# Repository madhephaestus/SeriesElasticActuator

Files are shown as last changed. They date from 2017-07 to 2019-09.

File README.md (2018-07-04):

# SeriesElasticActuator
A cad generator for series elastic actuator modules

# Prerequisites

PC with Ubuntu 16.04 64 bit, 16gb of ram and a discrete graphics card with OpenGL 3.2+ support. 
# Start Simulation
To simulate and control the arm, after programming and calibrating the arm (see notes in FW comments, calibrating the zeros of the arm is lab one) run BowlerStudio
From here: 
http://commonwealthrobotics.com/#downloads
or directly from the PPA:
	sudo add-apt-repository ppa:webupd8team/java
	sudo add-apt-repository ppa:mad-hephaestus/commonwealthrobotics -y
	sudo apt-get update
	sudo apt-get remove arduino bowlerstudio 
	sudo apt-get install bowlerstudio oracle-java8-set-default oracle-java8-installer arduino-ide
To open the arm, run BowlerStudio and From the Add 

Device Menu-> Creatures -> Hephaestus Arm

This will open a simulation of the arm. 
# Build an arm work cell
The BOM and printable files are here: https://github.com/madhephaestus/SeriesElasticActuator/releases/tag/0.1.6
The 3d printed parts should be printed at 60% infill. The SVG should be cut from 6.1mm wood (roughly !/4 inch). Assembly instruction document is here:
https://github.com/madhephaestus/SeriesElasticActuator/blob/master/assembly/RBE3001_Robot_Assembling_Guide.pdf
Its missing the intermediate step assemblies, with the load cell, make sure you have a dowel pin in the middle of the link, and rout the load cell wires up through the washer along the shaft. 
## Off The Shelf ( OTS ) electronics Alternate build
For a full OTS build, you can replace the Axis Encoder Board (custom board) with One of these:
https://www.digikey.com/product-detail/en/ams/AS5055A-QF_EK_AB/AS5055A-DK-AB-ND/4764625
and one of these: 
https://www.sparkfun.com/products/13879

You will need to modify the FW to use the I2c load cell. If you choose not to use the load cell, you will still need the device installed for the mechanical system to work. 

The Motherboard can replaced with hand wiring a breadboard using the wiring information in this file:
https://github.com/WPIRoboticsEngineering/RBE3001_nucleo_firmware/blob/master/src/main.h

# Firmware
The firmware for the nucleo can be found here:
https://github.com/WPIRoboticsEngineering/RBE3001_nucleo_firmware

Follow the instructions in the readme to setup and install the firmware. 

The arm needs to be calibrated out of the box, the orientation of the magnet is unknown at the time of assembly, so you need to change one line in the header file of the firmware. That value is derived by placing the arm in the home position, indicated by the pose the simulation starts up in. These values should be read as zero, but will have some random value based on how the magnet is glued in. 
# Connect Arm to Kinematics and Simulation
To launch the hardware interface, in BowlerStudio in the My Devices tab, click Disconnect all. Then open 

File Menu->Load File->gitcache/github.com/madhephaestus/SeriesElasticActuator/FullHardwareLaunch.groovy		

You will see a green Run button for the file, click that with the nucleo connected to the computer. It will load the model of the arm again, except this time the position of the arm will come from the hardware. To set set points in the tab called HephaestusWorkCell, expand the Arms menu and click on Hephaestus Arm, expand Current Position and use the slider or type values to move the arm.

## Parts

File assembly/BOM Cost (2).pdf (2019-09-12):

# 3001 Hephaestus Arm

### 1.0 Unit(s)

# Cost Structure

Raw Materials | Quantity | Unit Cost | Total Cost
30KG Large Torque 360° High Voltage Digital Servo | 3.0 Unit(s) | $ 18.00 | $ 54.00
R8 Bearing | 6.0 Unit(s) | $ 1.39 | $ 8.34
Steel Dowel Pin 2" | 3.0 Unit(s) | $ 0.36 | $ 1.08
Lulzbot PolyLite PLA 3mm (1 Gram) | 825.0 gram(s) | $ 0.03 | $ 24.75
NUCLEO-F746ZG | 1.0 Unit(s) | $ 24.47 | $ 24.47
Strain gauge Load Cell - 10kg, Straight Bar | 3.0 Unit(s) | $ 6.95 | $ 20.85
Steel Dowel Pin 2" | 5.0 Unit(s) | $ 0.36 | $ 1.80
M4 x 40mm | 1.0 Unit(s) | $ 0.12 | $ 0.12
M5 x 30mm | 16.0 Unit(s) | $ 0.74 | $ 11.84
M2 x 10mm | 12.0 Unit(s) | $ 0.16 | $ 1.92
USB A MALE TO MICRO B MALE 3' | 2.0 Unit(s) | $ 2.48 | $ 4.96
Small BreadBoard | 1.0 Unit(s) | $ 4.50 | $ 4.50
USB Logic Analyzer | 1.0 Unit(s) | $ 16.99 | $ 16.99
M3 x 10mm | 8.0 Unit(s) | $ 0.07 | $ 0.56
Sony PlayStation Eye Camera | 1.0 Unit(s) | $ 6.99 | $ 6.99
M5 x 8mm | 12.0 Unit(s) | $ 0.09 | $ 1.08
Axis Encoder Board | 3.0 Unit(s) | $ 75.00 | $ 225.00
Nucleo-144-Motherboard | 1.0 Unit(s) | $ 20.00 | $ 20.00
Rubber feet | 8.0 Unit(s) | $ 2.50 | $ 20.00

M5 x 100mm | 4.0 Unit(s) | $ 0.76 | $ 3.04
M5 x 75mm | 10.0 Unit(s) | $ 0.15 | $ 1.50
M5 Steel Nylon-Insert Locknut | 18.0 Unit(s) | $ 0.04 | $ 0.72
M3 x 6 mm | 3.0 Unit(s) | $ 0.08 | $ 0.24
M5 x 45mm | 4.0 Unit(s) | $ 0.14 | $ 0.54
1/4 in. 3'x2' PureBond Birch Plywood | 1.0 Unit(s) | $ 27.92 | $ 27.92
Jx pdi-6221mg 20 Kg Servo | 1.0 Unit(s) | $ 9.75 | $ 9.75
Total Cost of Raw Materials | $ 492.96

# 3001 Hephaestus Arm

### 1.0 Unit(s)

# Cost Structure

Raw Materials | Quantity | Unit Cost | Total Cost

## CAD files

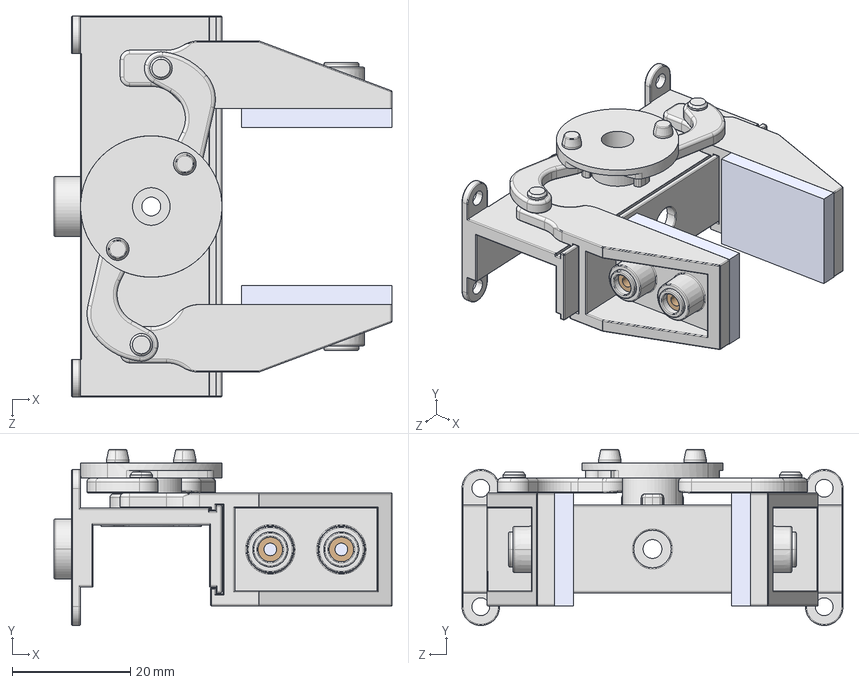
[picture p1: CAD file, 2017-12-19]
gripper/grip assembly.STEP
57.1 x 29.7 x 64.4 mm
Spirol INS 20-M3-.226 x 4
gripper finger pad x 2
gripper wheel
gripper arm x 2
gripper finger right
gripper wrist
gripper finger left

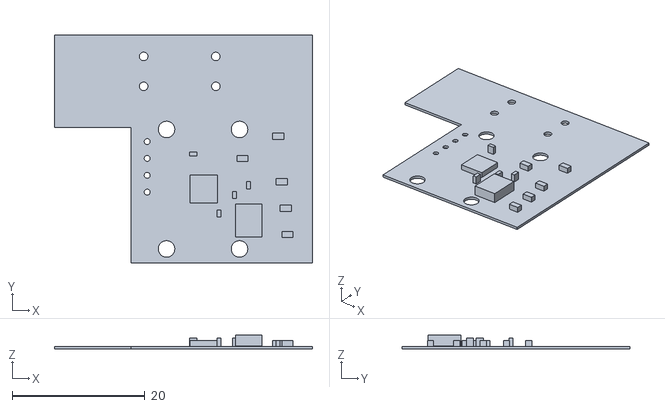
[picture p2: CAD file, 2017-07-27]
encoderBoard.stl
38.9 x 34.4 x 2.16

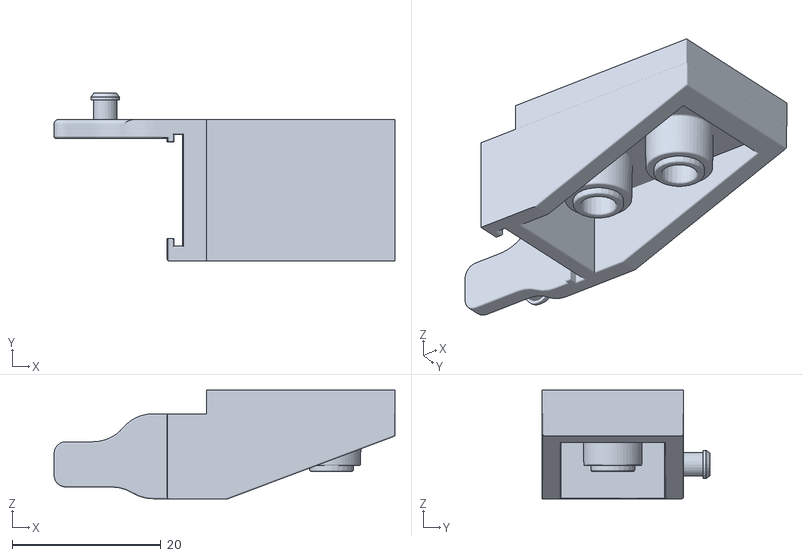
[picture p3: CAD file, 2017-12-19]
gripper/left.stl
45.9 x 22.6 x 14.6

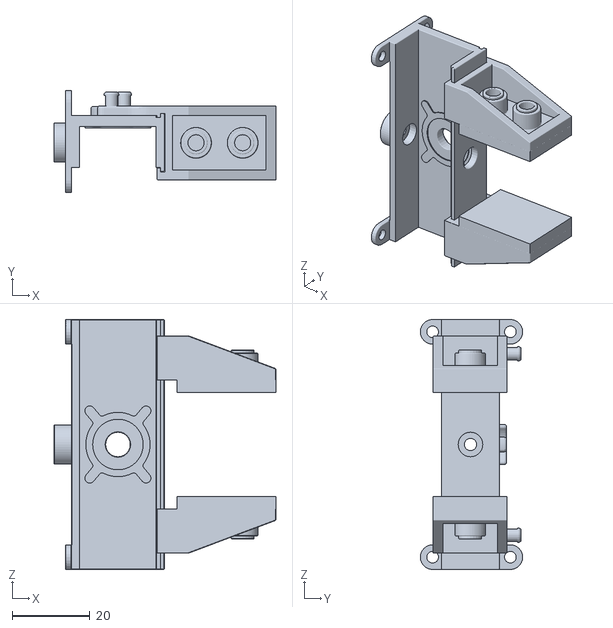
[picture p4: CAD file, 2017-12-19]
gripper/all.stl
57.1 x 26.4 x 64.4

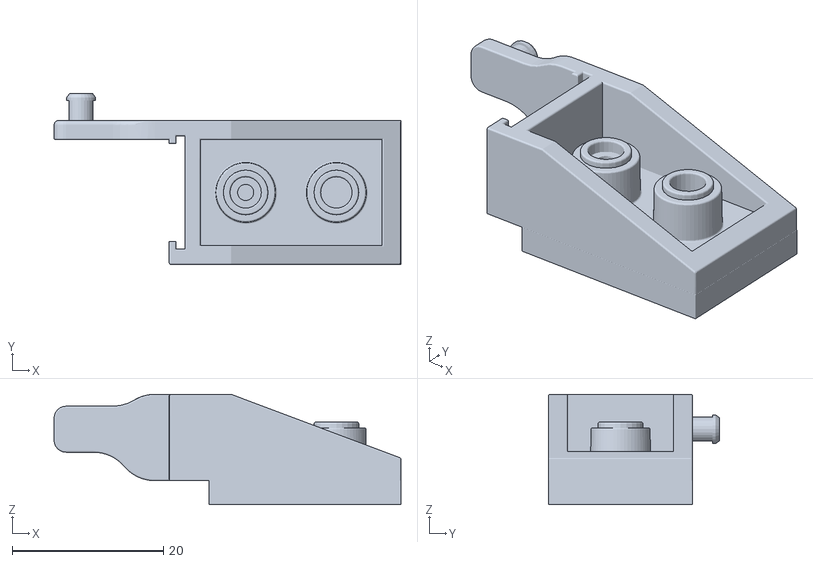
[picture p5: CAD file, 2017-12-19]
gripper/right.stl
45.9 x 22.6 x 14.6

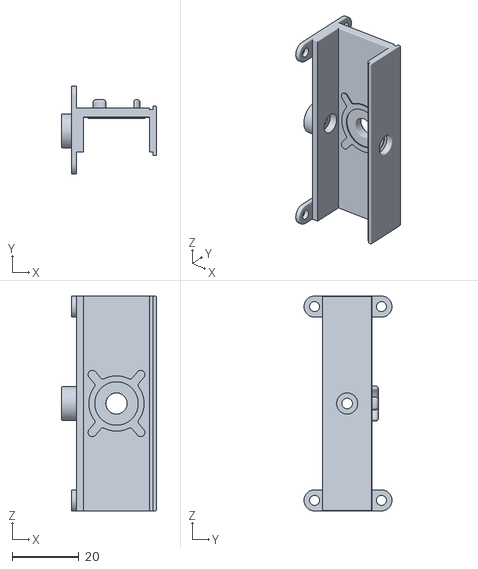
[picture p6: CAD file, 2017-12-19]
gripper/body.stl
28.3 x 26.4 x 64.4

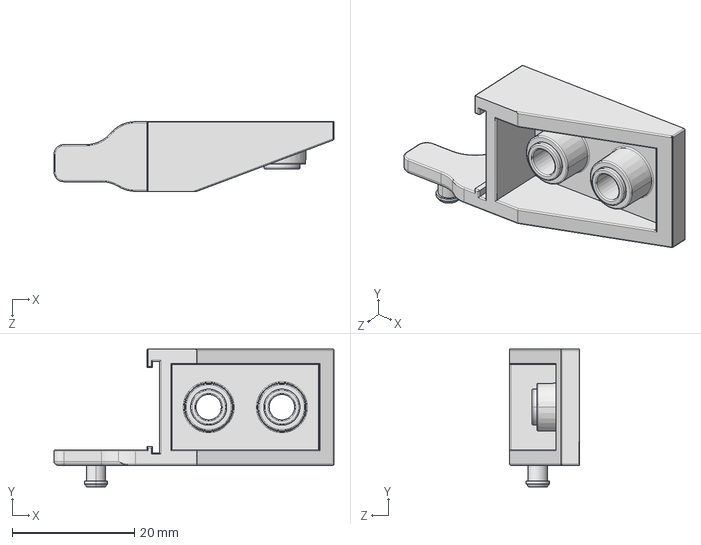
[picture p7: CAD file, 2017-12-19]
gripper/gripper finger left.STEP
45.9 x 22.6 x 11.4 mm

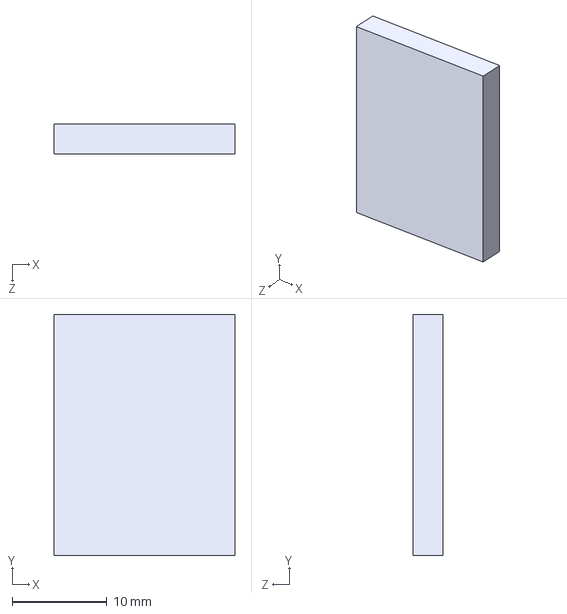
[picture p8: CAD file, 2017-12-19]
gripper/gripper finger pad.STEP
19.0 x 25.4 x 3.17 mm

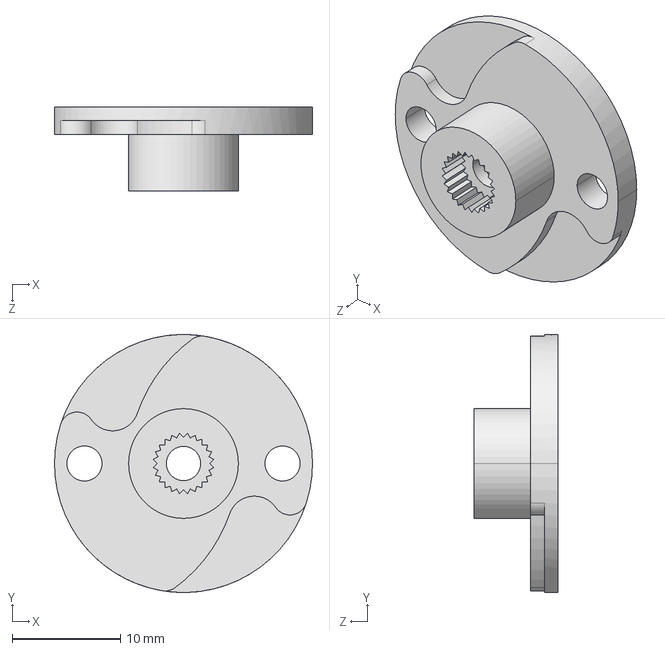
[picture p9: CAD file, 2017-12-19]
gripper/gripper wheel.STEP
23.9 x 23.9 x 7.80 mm

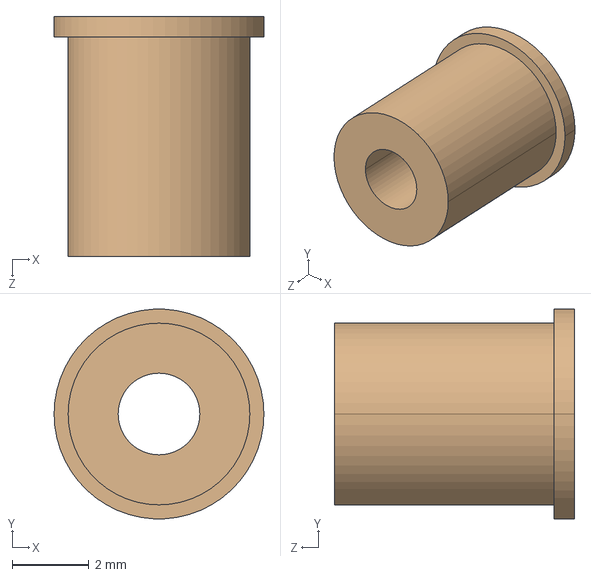
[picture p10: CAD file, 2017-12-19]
gripper/Spirol INS 20-M3-.226.STEP
5.49 x 5.48 x 6.27 mm

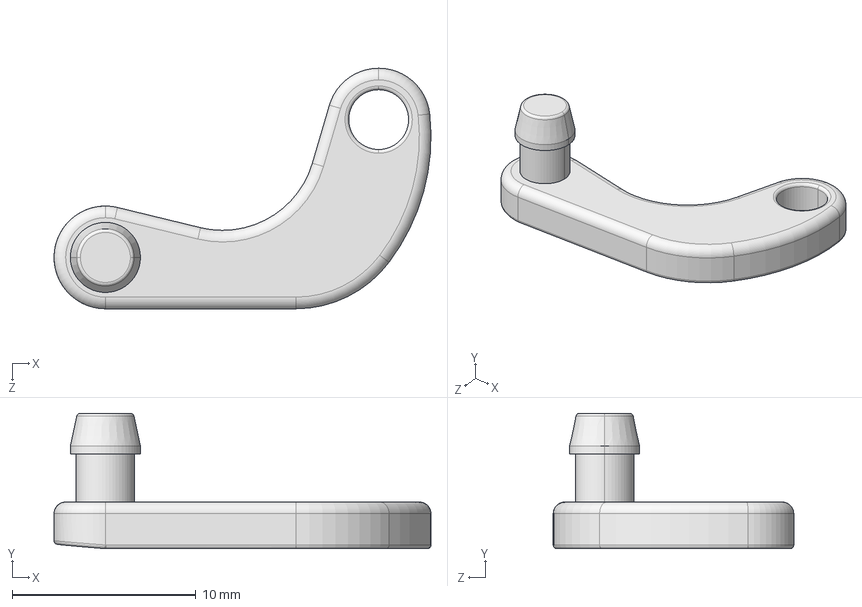
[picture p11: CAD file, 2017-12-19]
gripper/gripper arm.STEP
20.5 x 7.37 x 13.1 mm

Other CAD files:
gripper/gripper wrist.STEP
gripper/gripper finger right.STEP

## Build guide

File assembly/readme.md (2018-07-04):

See the PDF's in this directory for assembly instructions

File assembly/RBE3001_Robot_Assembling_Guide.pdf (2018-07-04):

## Robot assembly (After finishing all sub-assembly)

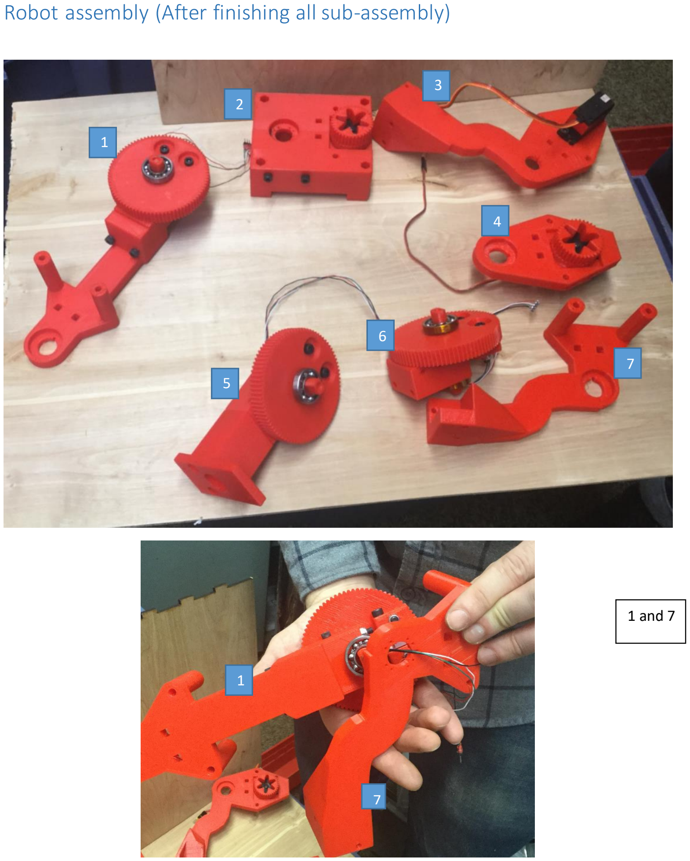
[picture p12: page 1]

1 and 7

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
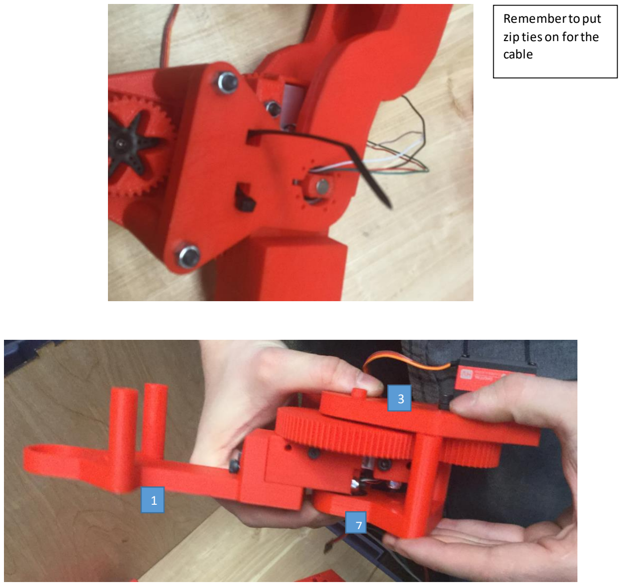
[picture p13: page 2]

Remember to put
zip ties on for the
cable

1

7

3

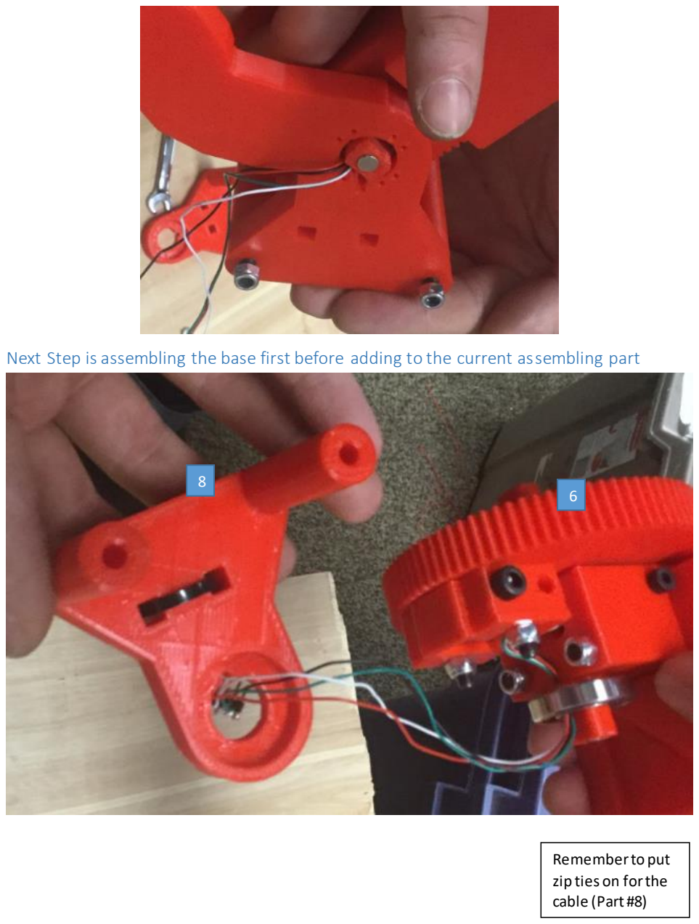
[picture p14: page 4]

Remember to put
zip ties on for the
cable (Part #8)

### Next Step is assembling the base first before adding to the current assembling part

8
6

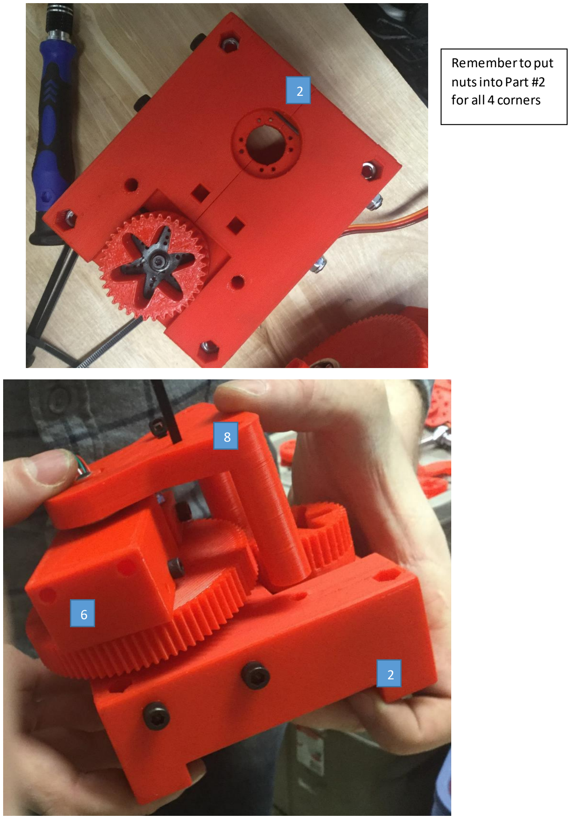
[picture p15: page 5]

Rememberto put
nuts into Part #2
for all 4 corners

8

6

2

2

Rememberto use
the hand tool for
this step.

### Next Step is attach the board to current base sub assembly

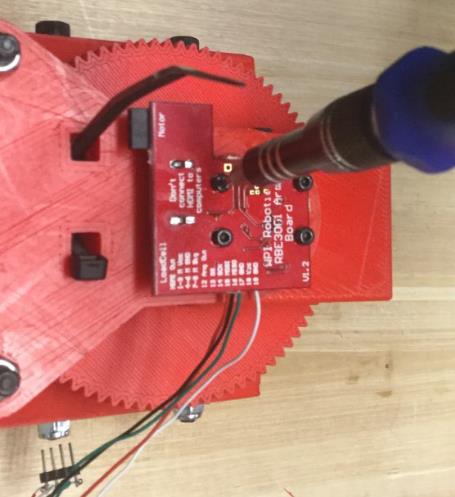
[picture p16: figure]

### Now attach the sub-assembly base to the middle link arm sub-assembly

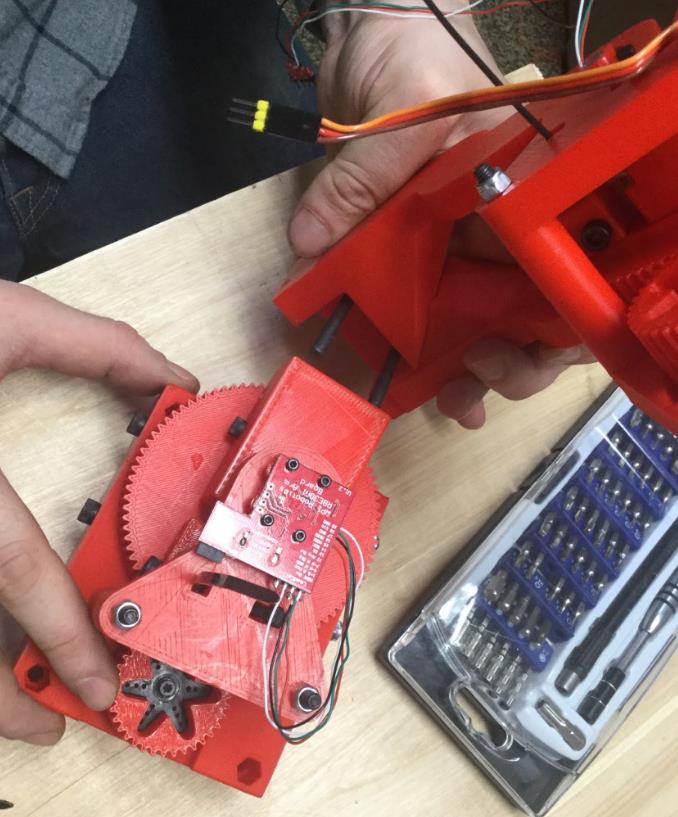
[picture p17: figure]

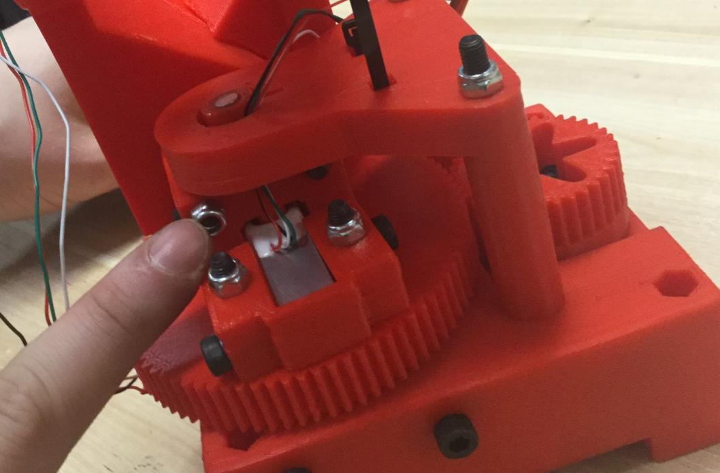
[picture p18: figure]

This picture was
taken without the
board attach to
the base sub-assembly

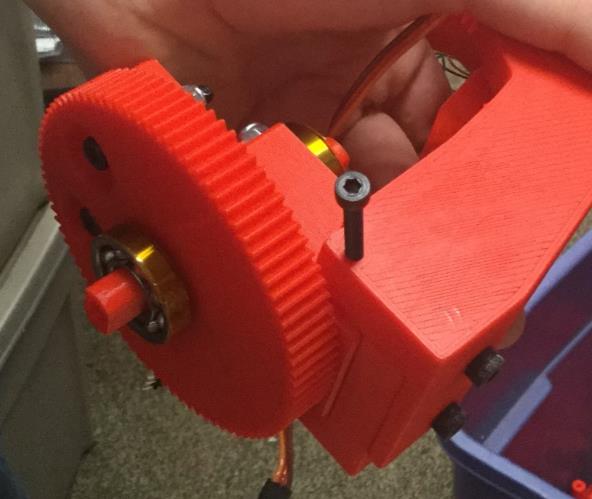
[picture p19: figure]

And adding this
screw to the side

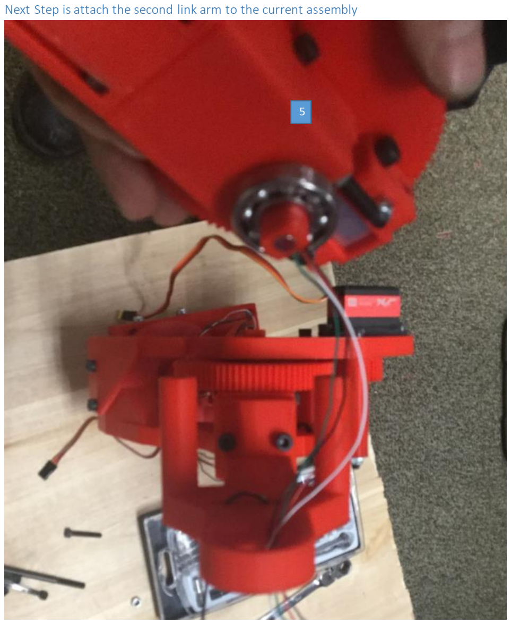
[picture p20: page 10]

### Next Step is attach the second link arm to the current assembly

5

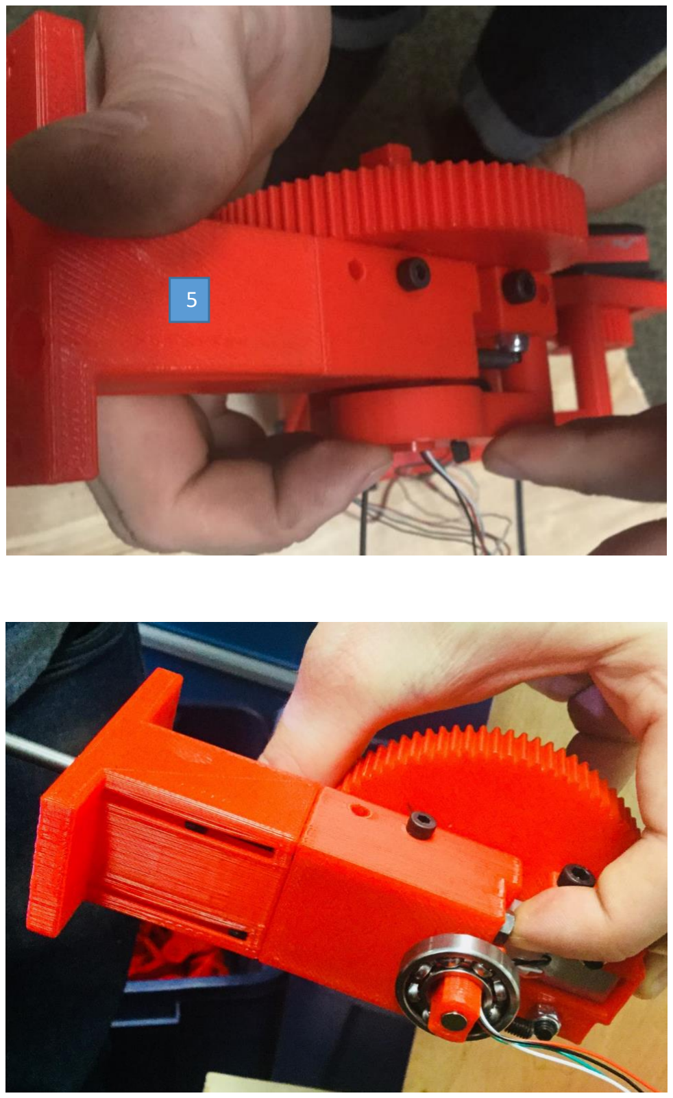
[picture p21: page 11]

5

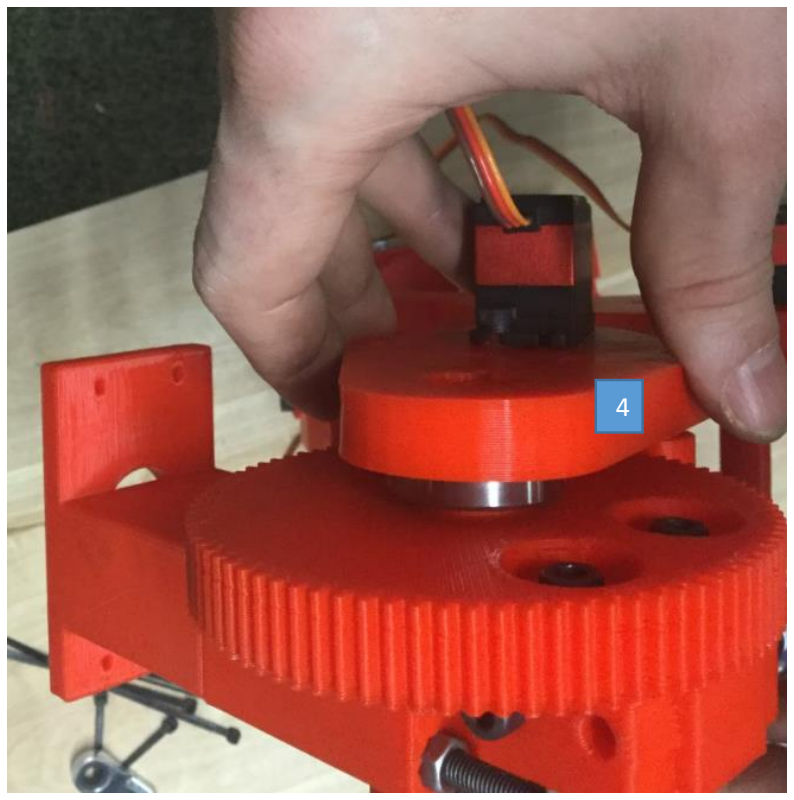
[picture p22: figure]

Attach part #4

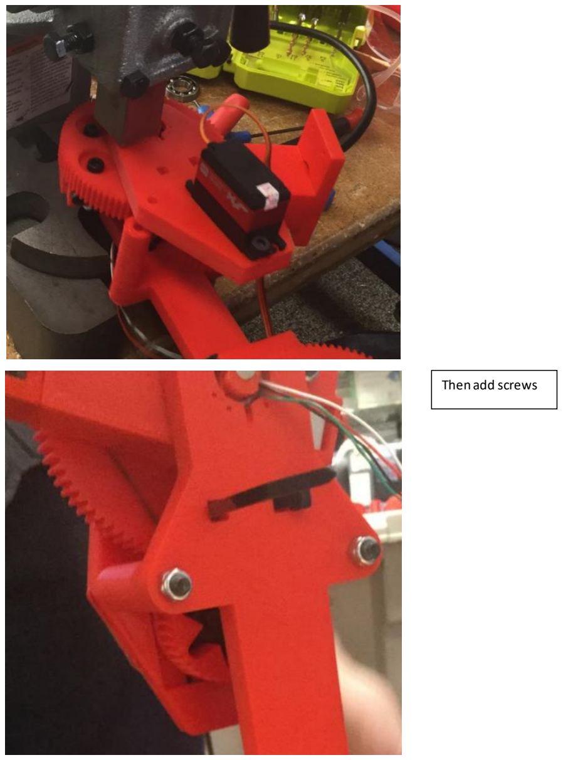
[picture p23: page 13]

Then add screws

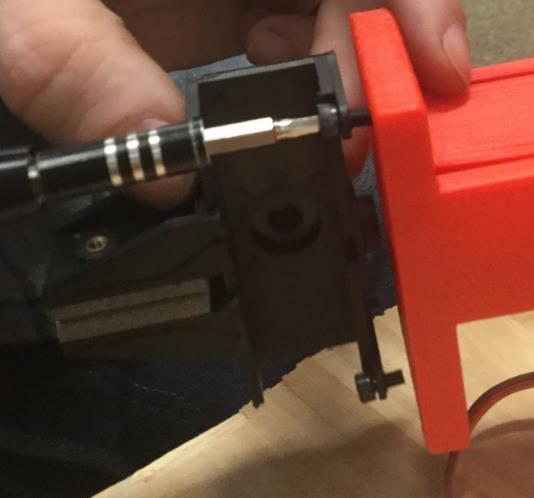
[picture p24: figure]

We need at least 3
screws

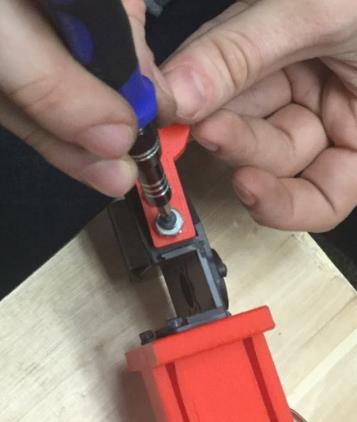
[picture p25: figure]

Use vex nuts for
bearings purpose

### Next Step is attach the gripper

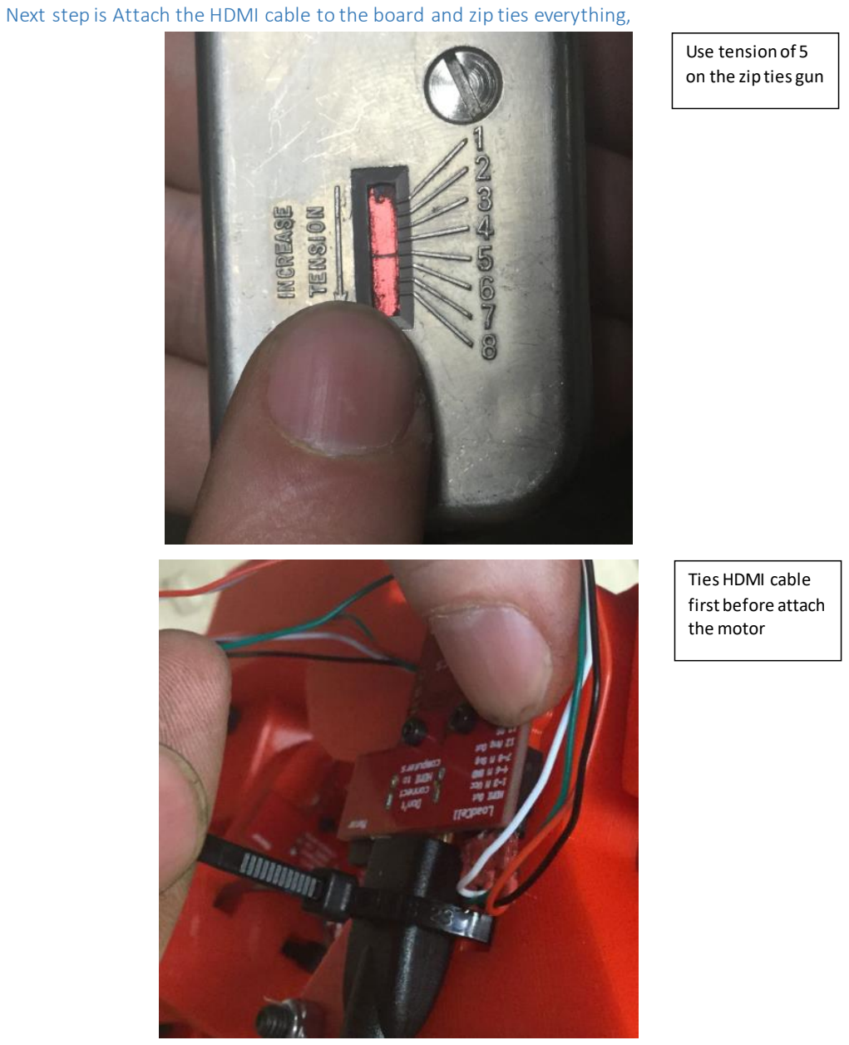
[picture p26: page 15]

Use tension of 5
on the zip ties gun

Ties HDMI cable
first before attach
the motor

Next step is Attach the HDMI cable to the board and zip ties everything,

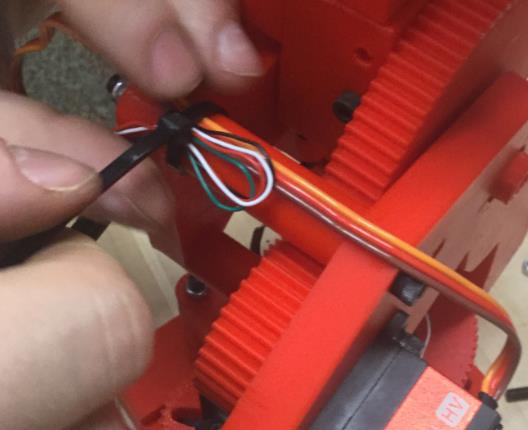
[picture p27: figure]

And we have finished assembling the Robot.

## Extra images: Sub-assembly

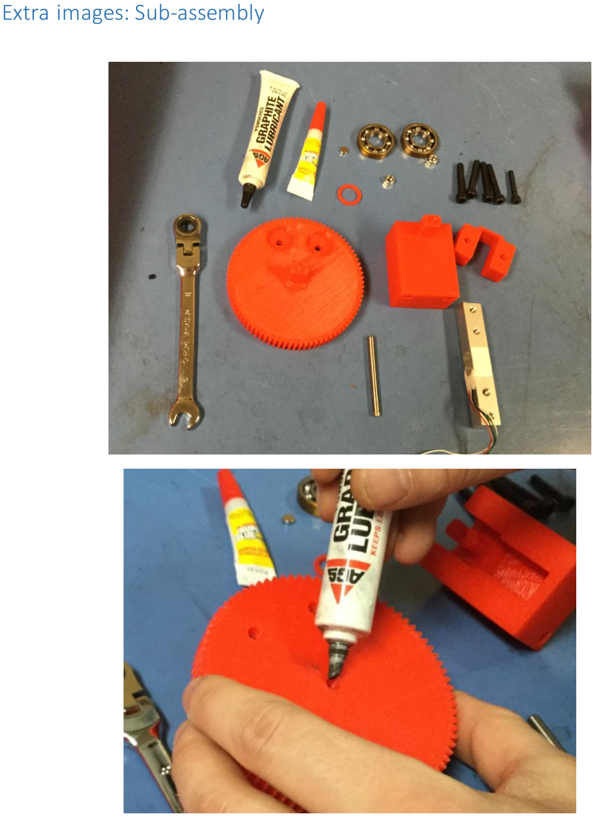
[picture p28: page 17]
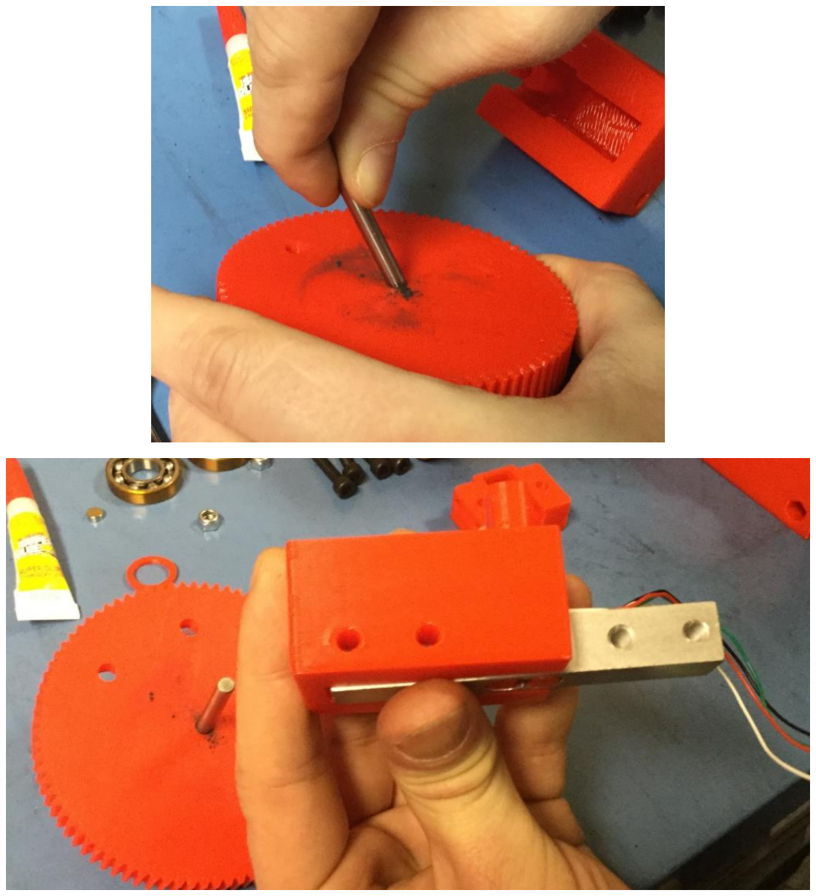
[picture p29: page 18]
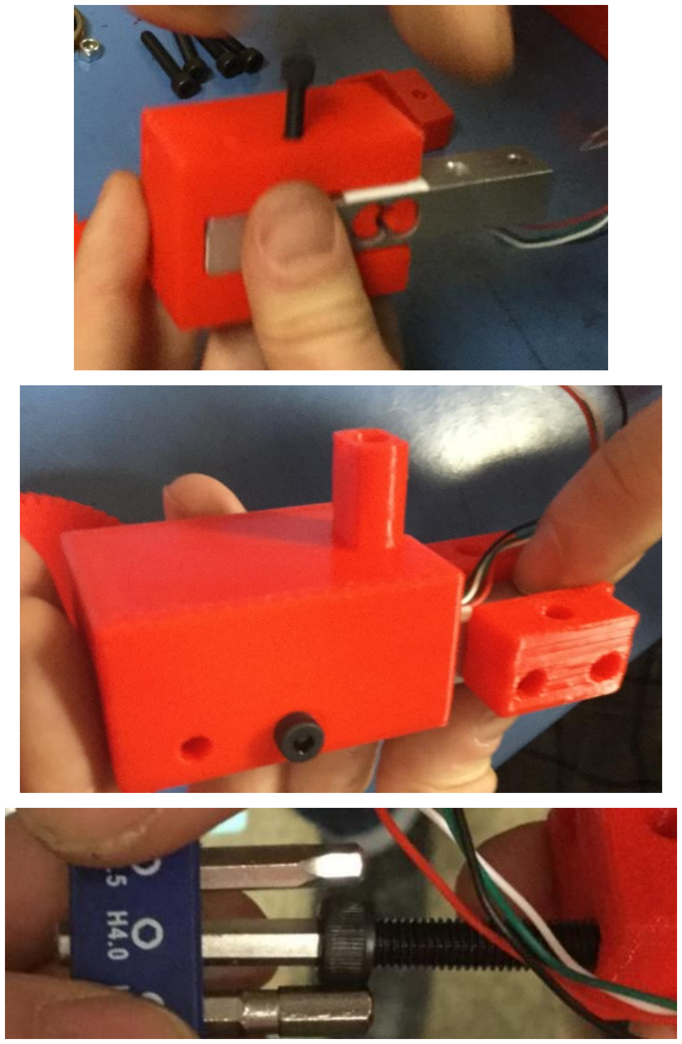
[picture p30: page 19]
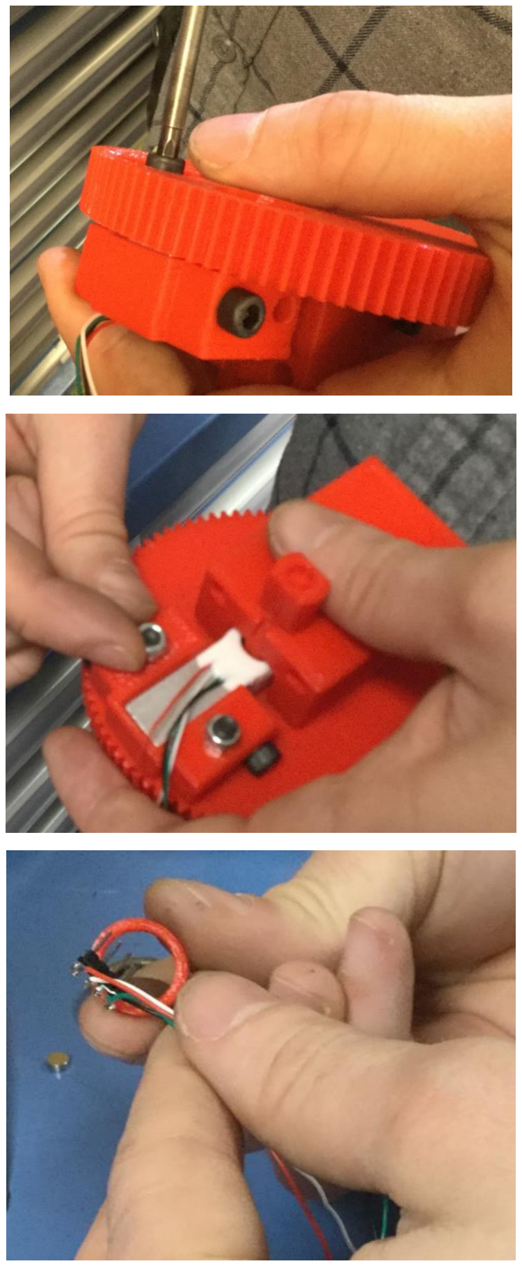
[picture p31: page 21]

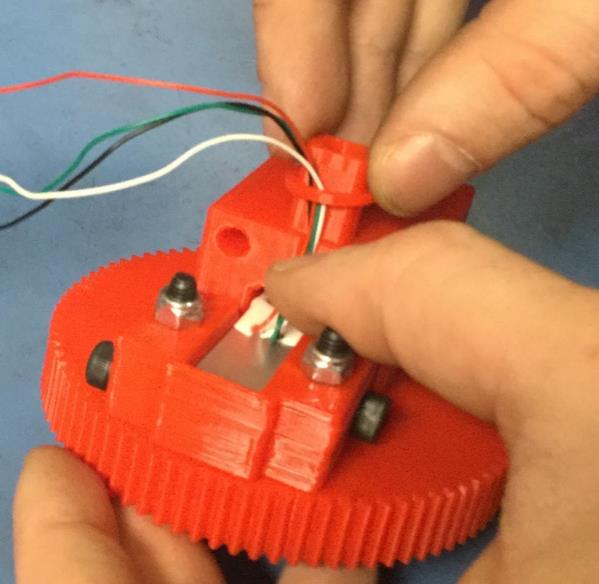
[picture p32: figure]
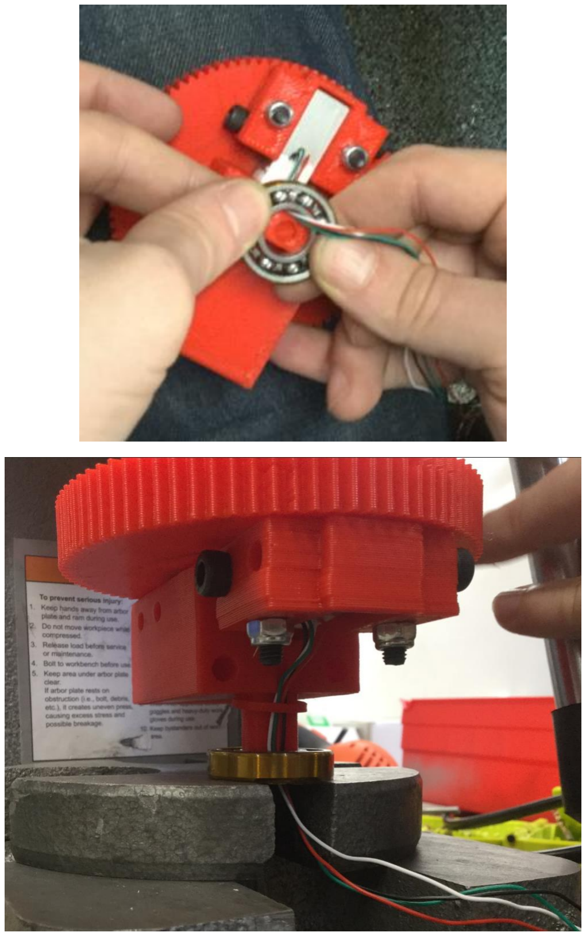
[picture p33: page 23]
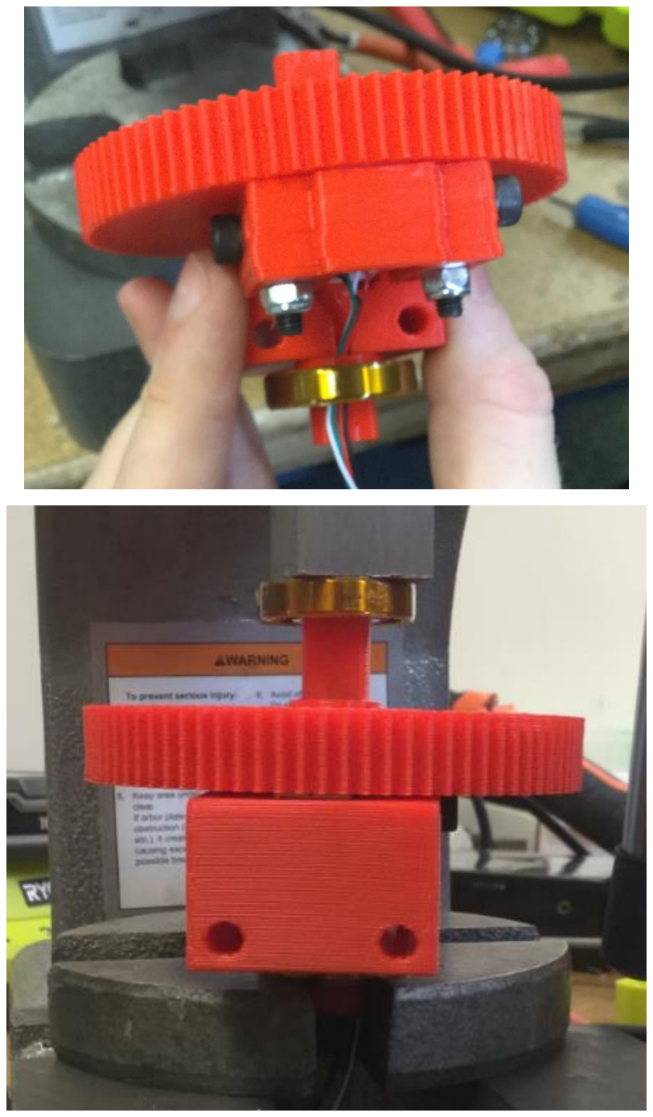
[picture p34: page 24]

Add Superglue

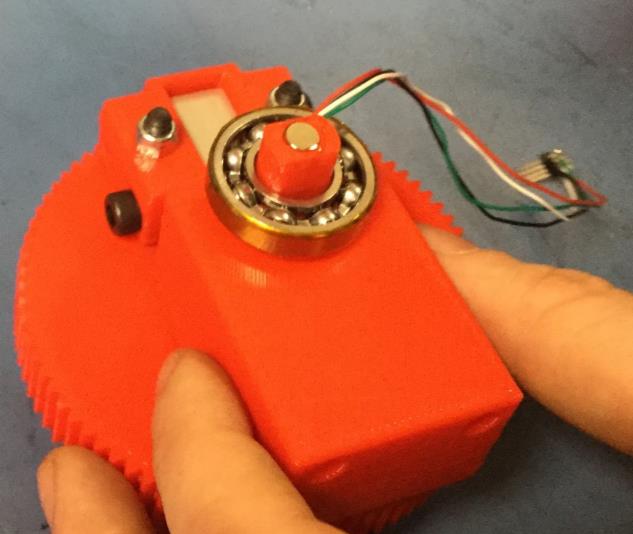
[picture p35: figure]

Put the
magnet in

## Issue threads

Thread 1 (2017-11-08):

Need washer to stand off links from bearings

madhephaestus, 2017-11-08:
The link blocks and gears are both touching the support brackets and causing friction. a small washer to standoff the link blocks from their bearings would fix the friction.

Closed 2018-10-03.

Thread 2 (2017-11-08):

Add a bushing for one side of link

madhephaestus, 2017-11-08:
The busing should replace the press fit used for the plastic pieces against the steel support pin.

Closed 2018-10-03.

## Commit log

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2017-02-16 smoother arm motion profile
2017-02-23 corrected kinematics
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2017-03-08 adding mount for the claw
2017-03-08 raising up the base of the arm
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2017-03-08 bearing and the encoder keepaway
    This is the complete keep away for one bearing/encoder unit
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2017-03-08 adding the printer offsets
2017-03-08 all keepaways for the printer offset created
2017-03-08 torsion spring loaded from vitamin data
2017-03-08 vitamin for the torsion spring working
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2017-03-08 loading the torsion spring
2017-03-09 rotated base spring out of workspacce
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2017-03-09 encoders should be in the links space
2017-03-09 configuration places tip on ground at home
2017-03-09 encoder squared keepaway set to constant
2017-03-09 adding printer offset to pin
2017-03-09 gears set back to the servo face
2017-03-09 loading bearing data from param
2017-03-09 loading bearing data from parameter
2017-03-10 adding the keepaway for the encoder
2017-03-10 adding the shaft to the keepaway
2017-03-10 Feed for the bottom of the base
    The bottom of the base now will not pinch wires comming out of the base
2017-03-10 added keepaway for shaft
2017-03-10 cap plate generator working
2017-03-11 bearing hol size termines the flats
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2017-03-11 adding the base gear back
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2017-03-13 round the hand plates
2017-03-13 fixed the encoder cache
2017-03-13 adding color to servo plate
2017-03-13 screw missing bearing
2017-03-14 adding the bezier extrusions
2017-03-14 full arm links being generated
2017-03-14 cutting the nub inside the bearing
2017-03-14 encoder cap as well
2017-03-14 adding come gear size options
2017-03-14 smaller servo for last link
2017-03-15 makes the top surface of the gear smoothly intersecting with the spring block
2017-03-15 make the holes go all the way through
2017-03-16 adding the links the pin and bushing
2017-03-16 updating the bearing types
2017-03-16 changign the pin dimentions
2017-03-20 printer offsets scaled to the amount it changes geometry
2017-03-20 adding the busing to the load bearing pin
2017-03-20 adding spring parametrics for printer offset
2017-03-20 move legs be the diameter
2017-03-20 updating the elbow servo
2017-03-23 spring calculated by height
2017-03-23 adding the offset for the spring height
2017-03-23 makinf the spring keepaway offset by the spring diameter change
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2017-03-25 added the keepaway for the spring using its actual keepaway zone
2017-03-29 making the legs longer
2017-03-29 updating the leg positions
2017-03-29 updating the bearing type
2017-04-10 A vitamin generator for conpression springs
2017-04-10 creating the spring vitamin
2017-04-10 adding printer offsets to model
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2017-04-12 this is the conpression spring and pins assembly
2017-04-12 screw holrd go sll yhr way through the base
2017-04-12 spring bolock should be cut out of the link
2017-05-03 updating kinematics and walking
2017-05-03 A cad model of the load cell and its keepaway zones
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2017-05-03 both bolts from top
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2017-05-04 using the parametric bolt size
2017-05-04 cutout for arm final link
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2017-05-08 adding offset for the length of the pin
2017-05-09 changing orentation of holes
2017-05-09 keepaway for the bolts
2017-05-09 keepaway for the bolts only
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2017-05-22 making the keepaway for the load cell sensor bigger
2017-05-26 adjusting the holes to match the measurments from the hand
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2017-06-07 a cad model for the 144 pin nucleo boards
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2017-06-07 adding the cut holes for hte nucleo board
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2017-07-19 the fuducial tp and hole in board should line up
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2017-07-26 Adding encoder .stl
    [encoderBoard.stl]
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2017-07-29 changing D-H parameters to make links clear encoder board
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2017-07-29 better bezier to avoid hitting the encoder
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2017-07-29 cutting link blocks on both sides for clean holes
2017-07-29 clearence for the load cell over the gears
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2017-08-01 fixed the bolt hole pattern
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2017-08-02 A model of the camera keep away zone
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2017-08-02 adding cutout and mfg scripts for camera mounts
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2017-08-05 nut should cut out by the flats not the points
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2017-08-07 corrected the servo top function
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2017-08-08 loading the arm servos using the ones we have in the lab
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2017-08-10 encoder in base needs to be set differently than the servo
2017-08-10 corrected the offset for the encoder
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2017-09-30 link cad cad generator working with new links
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2017-10-09 center pin on gear link now has no cutout for load cell
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2017-10-16 rotating the servo to allow nuts on the back of servo plate
2017-10-16 adding the cable cutout to the link block
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2017-11-10 washer offsets for bolt holes and body size
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2017-11-10 binding bolt standoff working
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2017-11-17 offset for zip ties avoid motor
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2017-11-18 motors backset to allign the mount plane with the print plane
    this should make the brackets easier to print by not needing any support
2017-11-18 adjusted kinematics to allow clearence for thre motor on the bottom
2017-11-19 straight line for the gear keepaway
    the rouded edge of the hole would make a blind overhang and fail to print
2017-11-19 nuts on big gear with clearence for nut driver
2017-11-20 correcting the limb cad engine
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2017-12-08 correcting kinematics
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2017-12-19 Adding gripper
    [Spirol INS 20-M3-.226.STEP, grip assembly.STEP, gripper arm.STEP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]
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2017-12-19 updated kinematics to deal with the calibration object
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2017-12-20 bolt holes alligned
    THe cups can be used to grab the balls and allign the arm to a known distance from the bed
2017-12-20 moving the bounding box down to clear the edge of the gripper
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2018-01-14 updated teh size of the work cell board to fit the motherboard
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2018-02-06 moving the base gear hole up to meet the gear
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2019-07-10 fixed gripper code
2019-07-15 fixed gripper func arg
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
